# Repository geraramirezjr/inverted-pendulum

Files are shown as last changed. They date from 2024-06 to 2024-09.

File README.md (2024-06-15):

# Inverted Pendulum
Project repository for a cart-pole inverted pendulum system. Designed hardware and software to support feedback control of belt gantry, DC motor, encoders, motor driver, and microcontroller. Developed a self swing up startup sequence and a double PID control algorithm with no external libraries that can successfully balance an inverted pendulum for 30+ seconds.

hero
Video files: [Swingup and Balance](images/swingup_and_balance.MOV), [Balance](images/balance.MOV)

## System Overview
System consists of a pendulum and encoder assembly driven via a linear belt gantry and DC motor controlled with an Arduino equivalent microcontroller.

### Electrical System
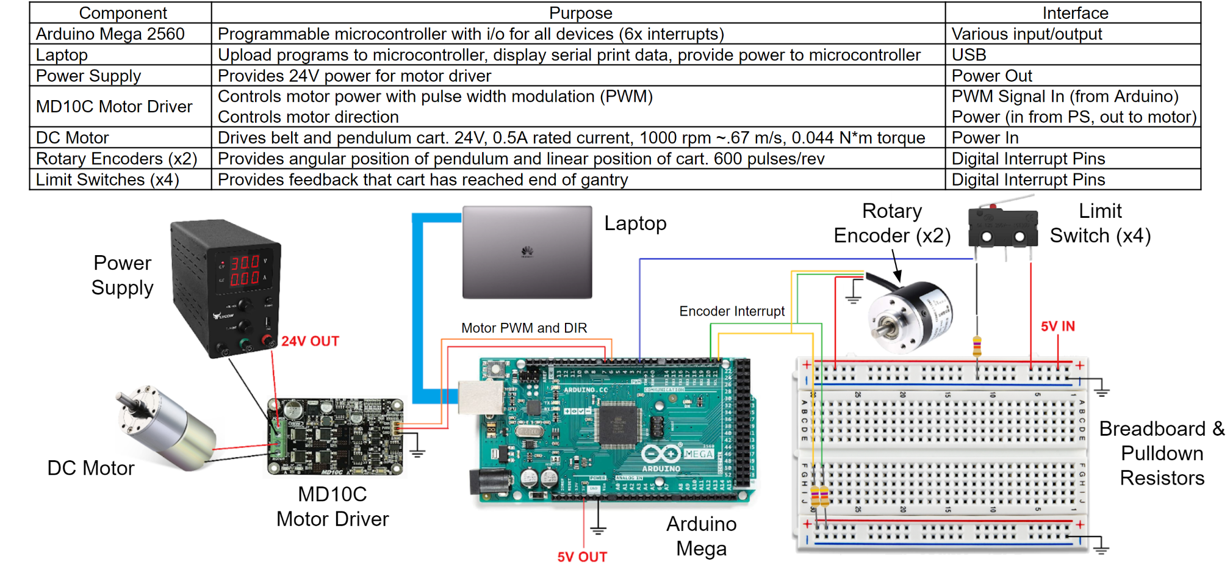
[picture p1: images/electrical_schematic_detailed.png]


### Mechanical Hardware
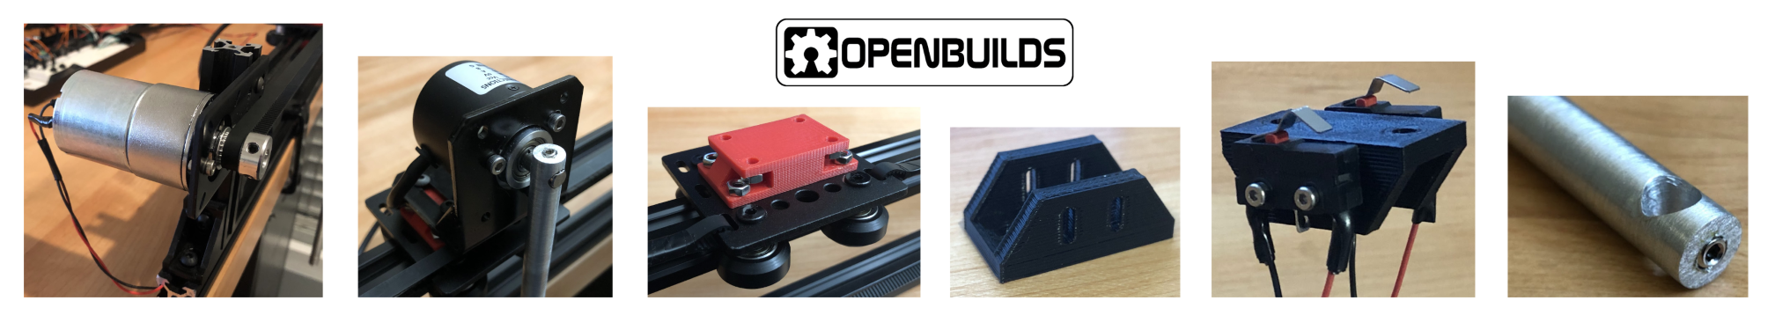
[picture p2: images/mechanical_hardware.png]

- [OpenBuilds](https://openbuilds.com/) Hardware: V-slot linear rail, V-slot gantry, brackets, fasteners, t-nuts
- Modified Stepper Brackets: DC motor and pendulum encoder mounting
- 3D Prints: Gantry and limit switch brackets
- Timing belt and pulleys
- Pendulum rod

## Software and Control

### Closed Loop Control

The main software loop running on the microcontroller consists of a double PID control scheme for pendulum angle and cart position. The previous error and current error for each position are used to perform numerical differentiation and numerical integration (midpoint integration). A combined error is then used to determine motor control. PID gains were heuristically determined with methods roughly similar to Ziegler–Nichols.

<p align="center">
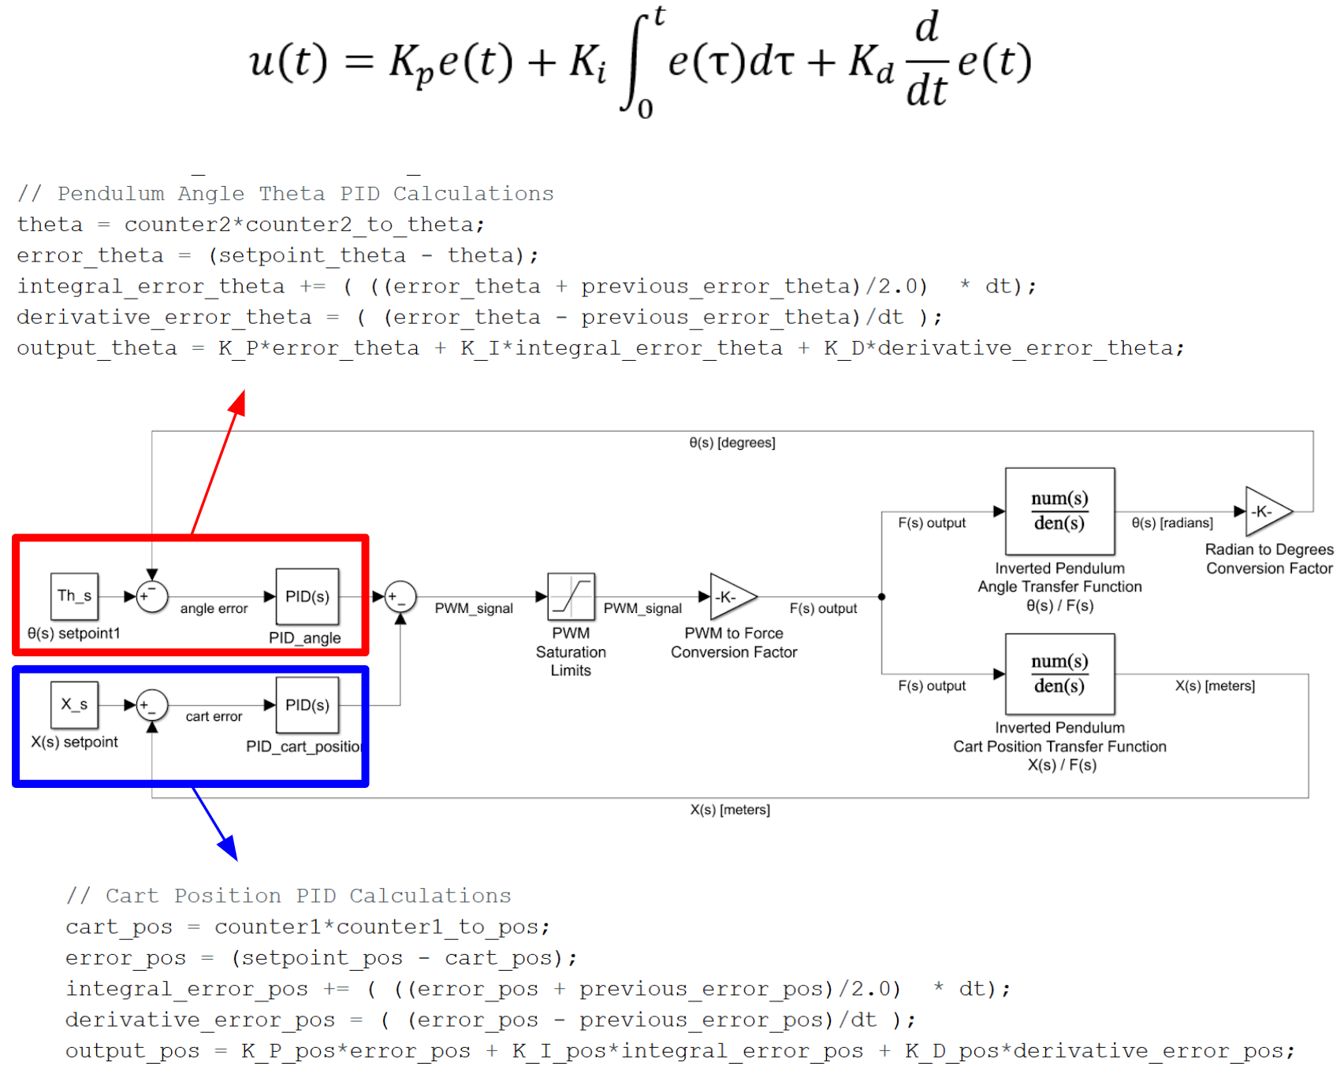
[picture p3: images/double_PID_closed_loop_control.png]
    
</p>

A few functions are used in support of the main loop operation:
- Motor Function: Used to control motor direction and current with a PWM signal
- Encoder Functions: Interrupt pins on the arduino are used to increment or decrement the encoder count
- Limit Switches: Used for system safety. If any limit switch interrupt is triggered, motor current set to zero.

### Swing Up Program

An initial swing up program is used to bring pendulum from dead hang to an inverted position. Desired swing up behaviour can roughly be viewed as a growing oscillatory sin wave where pendulum swings with more and more force from left to right and eventually snaps into a control loop once upright. Once inverted the program does not immediately enter the main double PID loop, but instead enters a single PID loop just controlling the pendulum angle. During testing the single PID control proved to be more robust to catching a swing up, and once stable the program continues to the main loop.

<p align="center">
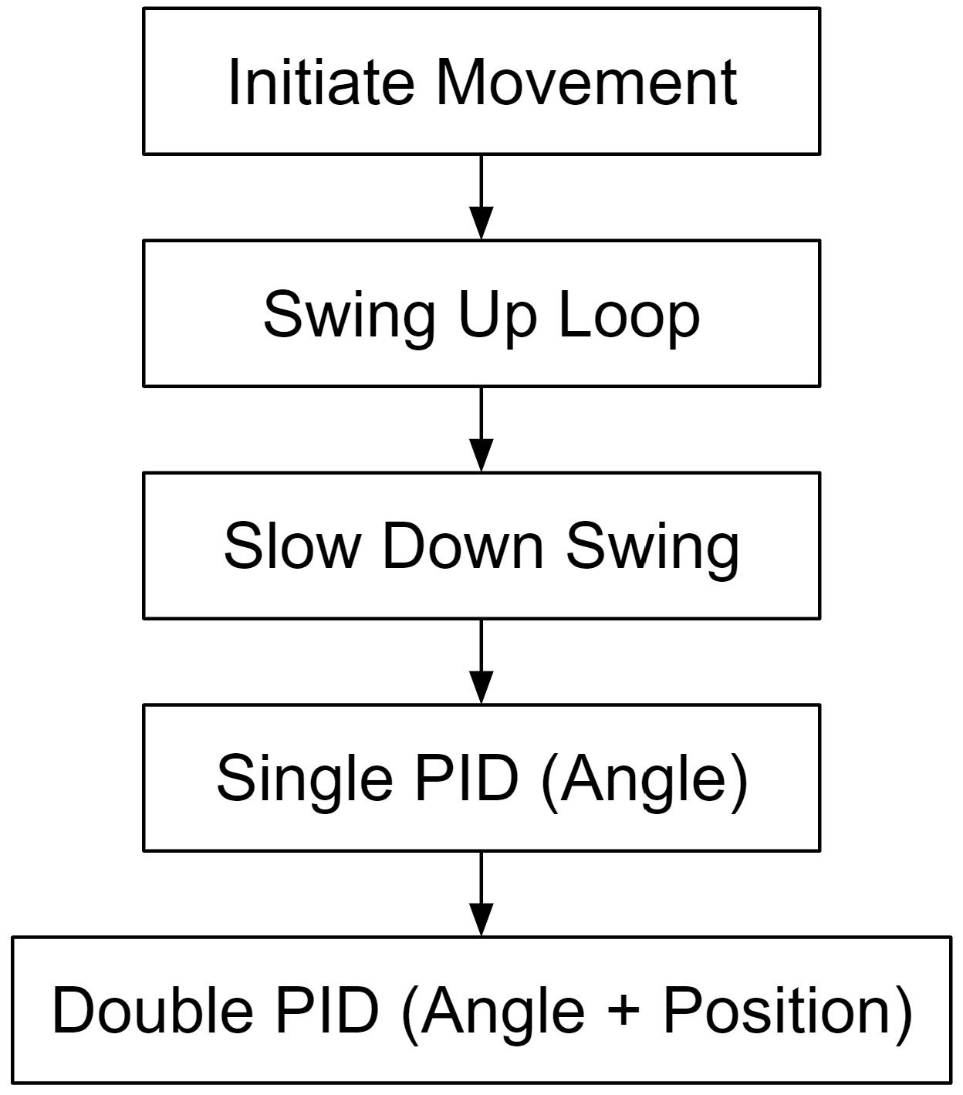
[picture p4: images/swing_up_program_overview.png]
    
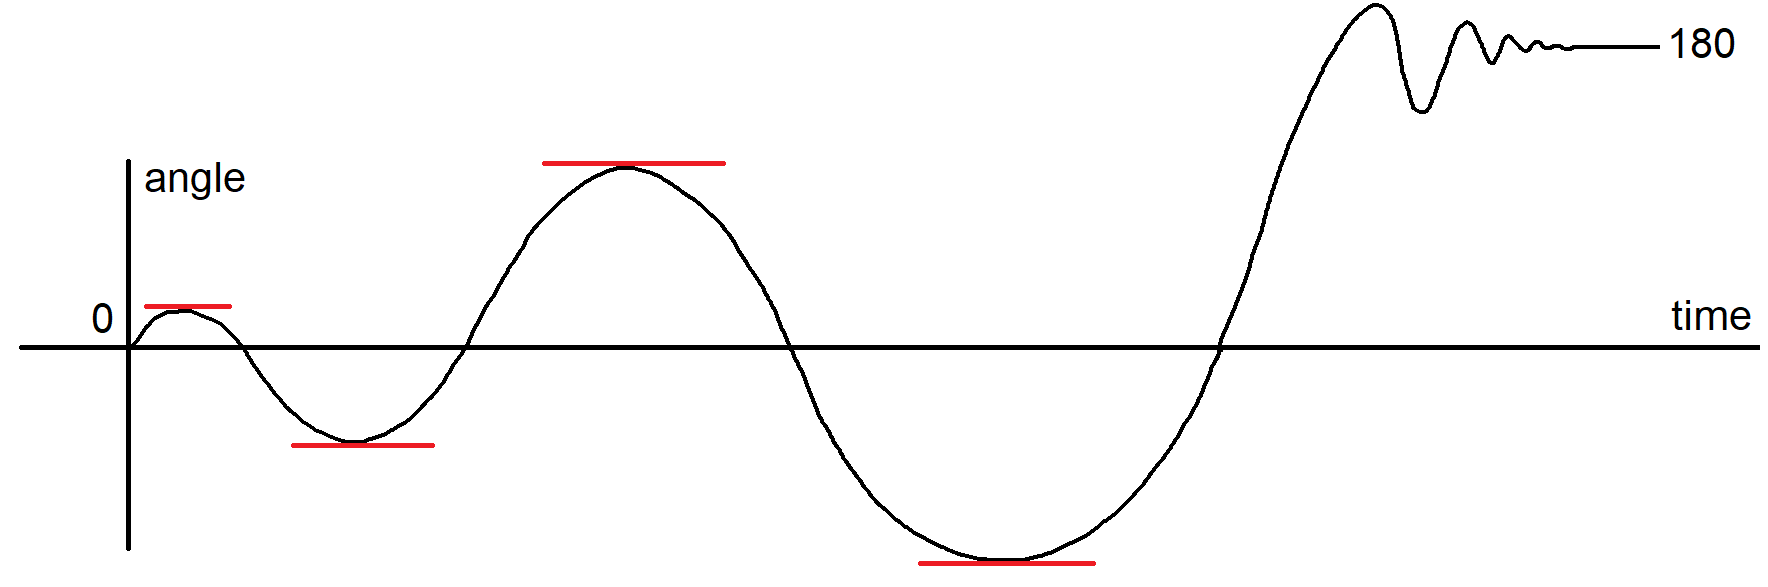
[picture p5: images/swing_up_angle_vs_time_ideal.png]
    
</p>

### Balancing
hero

## Misc. Images

Motor soldering

<br />

Limit switch wiring EMI shielding. Had an issue with intermittent system shutdowns and root caused the problem to motor EMI noise causing interrupts to switch. Wire shielding resolved issue.

<br />

Motor winding overcurrent damage when system railed during testing. Led to the development of limit switch safety features to prevent this failure mode.

<br />

Limit switch bracket


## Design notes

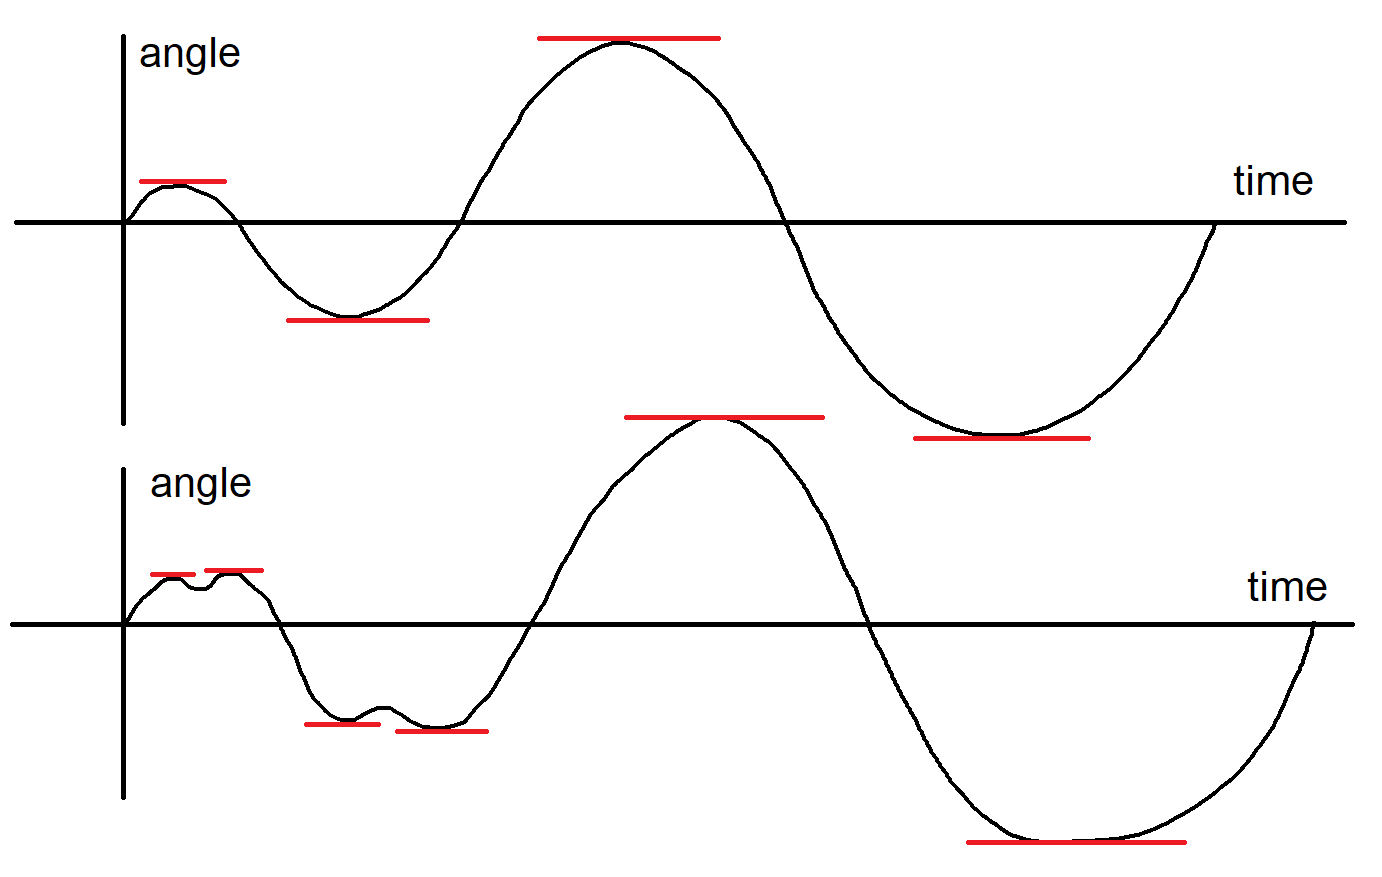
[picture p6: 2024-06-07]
images/swing_up_angle_vs_time.png

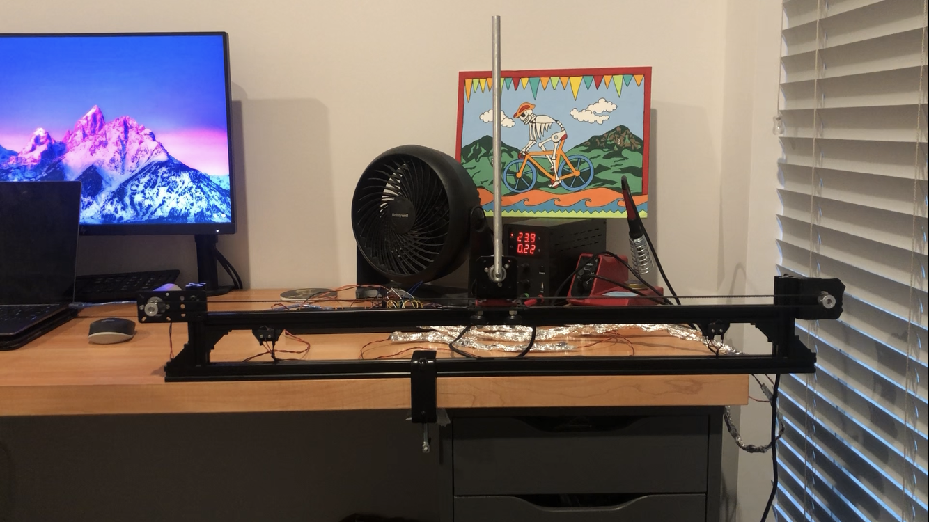
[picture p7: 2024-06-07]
images/inverted_pendulum.png

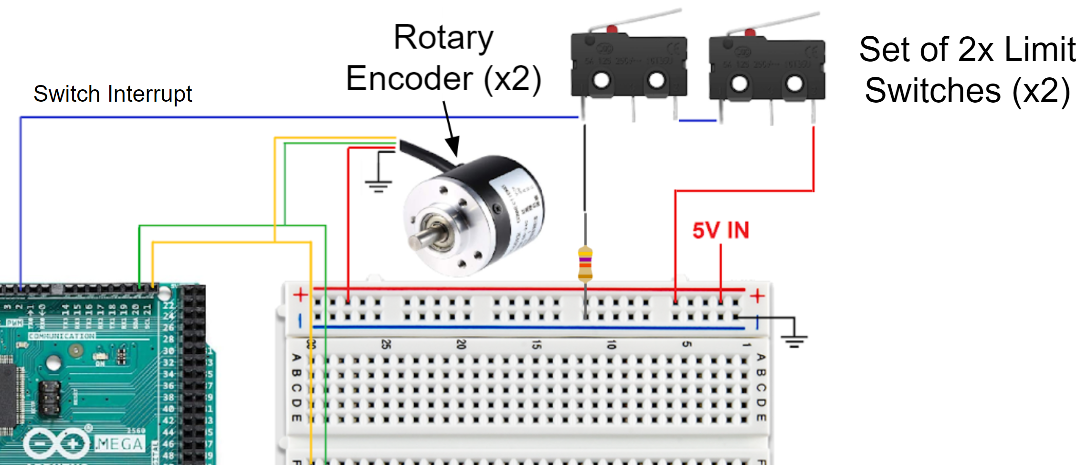
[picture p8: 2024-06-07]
images/limit_switch_detailed.png

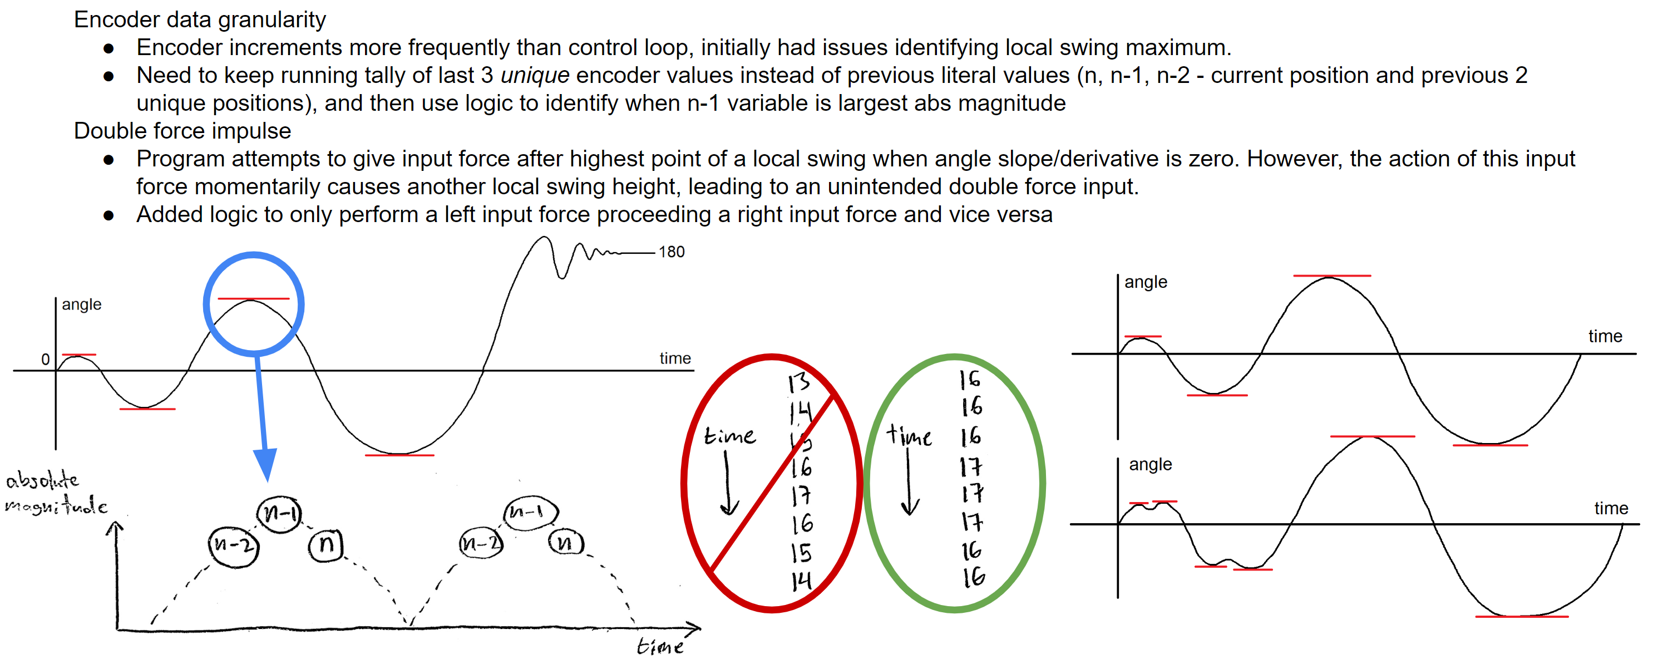
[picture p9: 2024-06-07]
images/swing_up_program_challenges.png

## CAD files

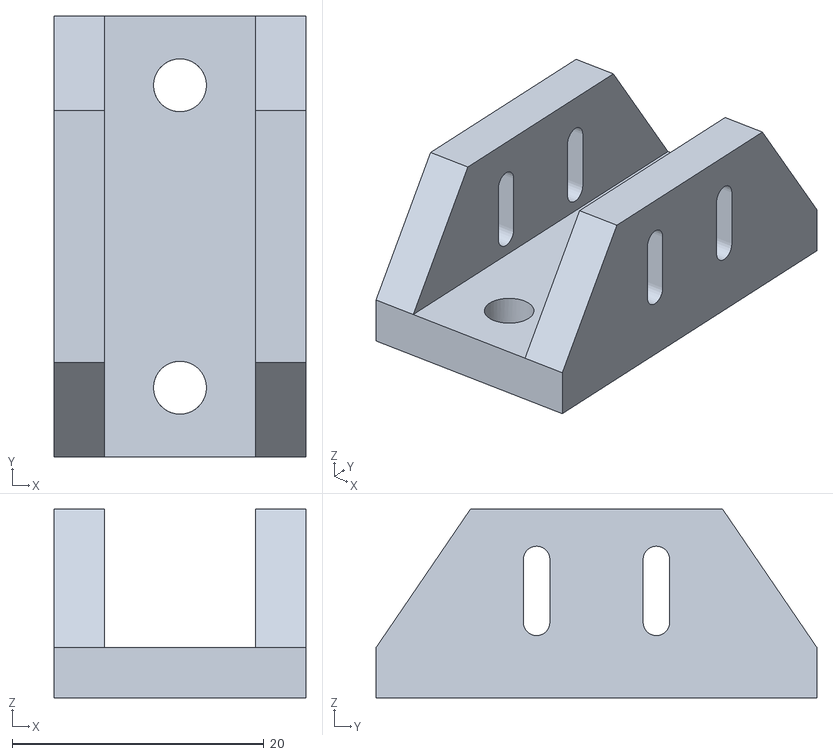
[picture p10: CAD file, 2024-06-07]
hardware/limit_switch_bracket_v2.stl
20.0 x 35.0 x 15.0

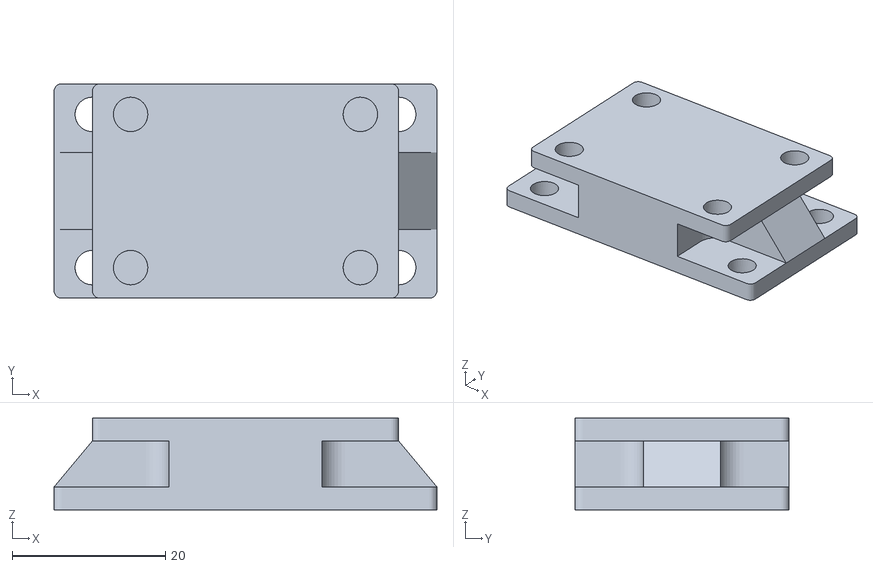
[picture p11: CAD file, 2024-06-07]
hardware/gantry_bracket_holder_v1.stl
50.0 x 28.0 x 12.0

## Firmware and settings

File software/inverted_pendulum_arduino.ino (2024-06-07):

// DC Motor Variables
#define pwm_Pin 7
#define dir_Pin 6
int pwm_value;
int mtr_dir_cmnd;

// Encoder Variables
#define outputA1 20
#define outputB1 21
#define outputA2 18
#define outputB2 19
volatile int counter1 = 0;
volatile int counter2 = -600;

// Swing Up Variables
volatile int counter2_bottom;
volatile int previous_counter2_bottom = 0;
volatile int previous_previous_counter2_bottom = 0;
volatile int n_counter2_bottom;
volatile int n_minus1_counter2_bottom = 0;
volatile int n_minus2_counter2_bottom = 0;
bool left_swing = 1;
unsigned long PID_angle_start_time;
unsigned long PID_angle_running_time = 0;
const float K_P_theta_Swing = 115.0;
const float K_I_theta_Swing = 0.8;
const float K_D_theta_Swing = 3.0;

// Control Variables
float theta;
float cart_pos;
const float counter1_to_pos = 20.0 * .02 / 1200.0;  // counter1 to position in meters
const float counter2_to_theta = 360.0 / 1200.0;     // counter2 to theta in degrees
const float setpoint_theta = 0;           // top dead center rotational position in degrees (180 degrees above still since counter1 starts at -180 degrees on calibration)
const float setpoint_position = 0; // center of gantry defined as intial linear position on startup
float error_theta = 0;
float integral_error_theta;
float derivative_error_theta;
float error_position = 0;
float integral_error_position;
float derivative_error_position;
float output_theta = 0;
float output_position = 0;
float output = 0;
unsigned long current_time;
unsigned long previous_time;
float previous_error_theta;
float previous_error_position;
const float K_P_theta = 70.0;//115.0;  //80.0;//80.0; //
const float K_I_theta = 0.9;//0.5; //0; //
const float K_D_theta = 4.8;//2.0; //8.73;//8.73; //
const float K_P_position = 585.0; //600.0;//300.0;  //50.0; // 100
const float K_I_position = 55.0; //70.0; //0.0;
const float K_D_position = 80.0; //135.0;  //10.0; //20
float dt;

// Limit Switches
#define right_switches_Pin 3
#define left_switches_Pin 2
volatile bool any_switch_triggered = false;
//volatile bool right_switches_triggered = false;
//volatile bool left_switches_triggered = false;


void setup() {
  // DC Motor Setup
  pinMode(pwm_Pin, OUTPUT);
  pinMode(dir_Pin, OUTPUT);

  // Encoders setup
  Serial.begin (57600);
  pinMode (outputA1, INPUT);
  pinMode (outputB1, INPUT);
  pinMode (outputA2, INPUT);
  pinMode (outputB2, INPUT);
  attachInterrupt(digitalPinToInterrupt(outputA1), pulseA1, RISING);
  attachInterrupt(digitalPinToInterrupt(outputB1), pulseB1, RISING);
  attachInterrupt(digitalPinToInterrupt(outputA2), pulseA2, RISING);
  attachInterrupt(digitalPinToInterrupt(outputB2), pulseB2, RISING);

  // Limit Switch Setup
  pinMode (right_switches_Pin, INPUT);
  pinMode (left_switches_Pin, INPUT);
  attachInterrupt(digitalPinToInterrupt(right_switches_Pin), trigger_right, FALLING);
  attachInterrupt(digitalPinToInterrupt(left_switches_Pin), trigger_left, FALLING);
  any_switch_triggered = false;

  // Delay
  delay(3000);

  // Swing Up (LOW moves right, HIGH moves left)
  while (any_switch_triggered == false && counter1 > -1000) {
    move_DC_motor(255, HIGH);
  }
  move_DC_motor(0, LOW);
  while ((counter2 + 600) < 0) {
    delay(1);
  }
  while (any_switch_triggered == false && counter2 < -200) {
    counter2_bottom = counter2 + 600;

    if (previous_counter2_bottom == counter2_bottom) {
      n_minus2_counter2_bottom = n_minus2_counter2_bottom;
      n_minus1_counter2_bottom = n_minus1_counter2_bottom;
      n_counter2_bottom = counter2_bottom;
    } else {
      n_minus2_counter2_bottom = n_minus1_counter2_bottom;
      n_minus1_counter2_bottom = previous_counter2_bottom;
      n_counter2_bottom = counter2_bottom;
    }

    if ( (abs(n_counter2_bottom) < abs(n_minus1_counter2_bottom)) && (abs(n_minus1_counter2_bottom) > abs(n_minus2_counter2_bottom)) && counter2_bottom < 0 && left_swing == 0) {
      move_DC_motor(255, HIGH);
      left_swing = 1;
      delay(183);
      move_DC_motor(0, LOW);
    }
    if ( (abs(n_counter2_bottom) < abs(n_minus1_counter2_bottom)) && (abs(n_minus1_counter2_bottom) > abs(n_minus2_counter2_bottom)) && counter2_bottom > 0 && left_swing == 1) {
      move_DC_motor(255, LOW);
      left_swing = 0;
      delay(183);
      move_DC_motor(0, LOW);
    }

    previous_previous_counter2_bottom = previous_counter2_bottom;
    previous_counter2_bottom = counter2_bottom;

  }

  // START OF JUST ANGLE PID FOR CATCHING SWING UP
  delay(70); // 90
  while (any_switch_triggered == false && counter2 < -150) {
    move_DC_motor(255, LOW);
  }
  //  move_DC_motor(255, LOW);
  //  delay(65);
  PID_angle_start_time = micros();
  while (any_switch_triggered == false && PID_angle_running_time < 300000) {
    // Control Calculations Using Pendulum Encoder Theta (counter2 encoder, clockwise positive) + Cart Position (counter1 encoder, left positive)
    // Time
    current_time = micros();
    dt = (current_time - previous_time) / 1000000.0;
    // Theta
    theta = counter2 * counter2_to_theta;
    error_theta = (setpoint_theta - theta);
    integral_error_theta += ( ((error_theta + previous_error_theta) / 2.0)  * dt);
    derivative_error_theta = ( (error_theta - previous_error_theta) / dt );
    output_theta = K_P_theta_Swing * error_theta + K_I_theta_Swing * integral_error_theta + K_D_theta_Swing * derivative_error_theta;
    // Combining PID control calculations for Pendulum Theta and Cart Position
    output = output_theta;
    // Assigning current PID variables for next loop
    previous_error_theta = error_theta;
    previous_time = current_time;

    // Run Motor Programs
    pwm_value = abs(output);
    if (pwm_value < 0) {
      pwm_value = 0;
    } else if (pwm_value > 255) {
      pwm_value = 255;
    }

    // motor direction logic
    if (output > 0) {
      mtr_dir_cmnd = HIGH;      // HIGH moves left
    } else if (output <= 0) {
      mtr_dir_cmnd = LOW;       // LOW moves right, arbitrarily included zero. note that if output/pwm value is zero motor won't move anyways.
    }

    // motor function logic
    if (counter2 < 200 && counter2 > -200) {       // < 0 counter2 pendlulum is left of top dead center, > 0 counter2 is right of top dead center
      move_DC_motor(pwm_value, mtr_dir_cmnd);
    } else {
      move_DC_motor(0, LOW);
    }

    // Time delay
    delayMicroseconds(1000);
    // PID Angle Running Time
    PID_angle_running_time = current_time - PID_angle_start_time;
  }
  /// END OF JUST ANGLE PID FOR CATCHING SWING UP
  counter1 = 0;
}

void loop() {

  while (any_switch_triggered == false) {
    //Serial.println("ENTERED MAIN CONTROL LOOP");
    // Control Calculations Using Pendulum Encoder Theta (counter2 encoder, clockwise positive) + Cart Position (counter1 encoder, left positive)
    // Time
    current_time = micros();
    dt = (current_time - previous_time) / 1000000.0;
    // Theta Pendulum Angle
    theta = counter2 * counter2_to_theta;
    error_theta = (setpoint_theta - theta);
    integral_error_theta += ( ((error_theta + previous_error_theta) / 2.0)  * dt);
    derivative_error_theta = ( (error_theta - previous_error_theta) / dt );
    output_theta = K_P_theta * error_theta + K_I_theta * integral_error_theta + K_D_theta * derivative_error_theta;
    // Cart Position
    cart_pos = counter1 * counter1_to_pos;
    error_position = (setpoint_position - cart_pos);
    integral_error_position += ( ((error_position + previous_error_position) / 2.0)  * dt);
    derivative_error_position = ( (error_position - previous_error_position) / dt );
    output_position = K_P_position * error_position + K_I_position * integral_error_position + K_D_position * derivative_error_position;
    // Combining PID control calculations for Pendulum Theta and Cart Position
    output = output_theta + output_position;
    // Assigning current PID variables for next loop
    previous_error_theta = error_theta;
    previous_error_position = error_position;
    previous_time = current_time;

    // Run Motor Programs
    pwm_value = abs(output);
    if (pwm_value < 0) {
      pwm_value = 0;
    } else if (pwm_value > 255) {
      pwm_value = 255;
    }

    // motor direction logic
    if (output > 0) {
      mtr_dir_cmnd = HIGH;      // HIGH moves left
    } else if (output <= 0) {
      mtr_dir_cmnd = LOW;       // LOW moves right, arbitrarily included zero. note that if output/pwm value is zero motor won't move anyways.
    }

    // motor function logic
    if (counter2 < 200 && counter2 > -200) {       // < 0 counter2 pendlulum is left of top dead center, > 0 counter2 is right of top dead center
      move_DC_motor(pwm_value, mtr_dir_cmnd);
    } else {
      move_DC_motor(0, LOW);
    }

    // Time delay
    //delay(2);
    delayMicroseconds(1000);
    //Serial.println(output);
    //    Serial.println(any_switch_triggered);

    // Serial Monitor (remember to uncomment Serial.begin line in setup)
    //    Serial.print(counter1);
    //    Serial.print("\t");
    //    Serial.print(counter2);
    //    Serial.print("\t");
    //    Serial.print(theta);
    //    Serial.print("\t");
    //    Serial.print(error_theta);
    //    Serial.print("\t");
    //    Serial.print(integral_error_theta);
    //    Serial.print("\t");
    //    Serial.print(derivative_error_theta);
    //    Serial.print("\t");
    //    Serial.print(error_position);
    //    Serial.print("\t");
    ////    Serial.print(integral_error_position);
    ////    Serial.print("\t");
    ////    Serial.print(derivative_error_position);
    ////    Serial.print("\t");
    //    Serial.print(output_theta);
    //    Serial.print("\t");
    //    Serial.print(output_position);
    //    Serial.print("\t");
    //    Serial.print(pwm_value);
    //    Serial.print("\t");
    ////    Serial.print(previous_time);
    ////    Serial.print("\t");
    ////    Serial.print(current_time);
    ////    Serial.print("\t");
    //    Serial.println(dt);

  }

  while (any_switch_triggered == true) {
    //stay in loop
    move_DC_motor(0, LOW);
    //    Serial.println("stuck in SWITCH TRIGGER  loop");
    //    Serial.println(any_switch_triggered);
    //Serial.println(counter2);
  }


}

// Move DC Motor (LOW moves right, HIGH moves left)
void move_DC_motor(float pwm_value, int motor_direction) {
  digitalWrite(dir_Pin, motor_direction);
  analogWrite(pwm_Pin, pwm_value);
}

// Encoders Interrupt pulses
void pulseA1() {
  if (digitalRead(outputB1) == LOW) {
    counter1 --;
  } else {
    counter1 ++;
  }
}
void pulseB1() {
  if (digitalRead(outputA1) == LOW) {
    counter1 ++;
  } else {
    counter1 --;
  }
}

void pulseA2() {
  if (digitalRead(outputB2) == LOW) {
    counter2 ++;
  } else {
    counter2 --;
  }
}
void pulseB2() {
  if (digitalRead(outputA2) == LOW) {
    counter2 --;
  } else {
    counter2 ++;
  }
}

// Limit Switch Interrupt
void trigger_right() {
  detachInterrupt(right_switches_Pin);
  any_switch_triggered = true;
}

void trigger_left() {
  detachInterrupt(left_switches_Pin);
  any_switch_triggered = true;
}
